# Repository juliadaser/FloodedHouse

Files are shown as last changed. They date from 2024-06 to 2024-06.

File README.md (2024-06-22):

# Flooded House

All files, code, and data used to build _**Flooded House**_.

Flooded House GIF

Art is for all! This GitHub page provides insight into my building process, and includes all files and code to make _Flooded House_ as transparent as possible. This is especially important because _Flooded House_ is a data visualization about climate change - a topic where accuracy and transparency are crucial.

## Important Links

- Read more about my project on [my website](https://www.juliadaser.com/flooded-house).
- Explore the data used for this project on [the NASA website](https://sealevel.nasa.gov/ipcc-ar6-sea-level-projection-tool).

## User Guide

1. 🛠️ Click [here](/Fabrication) for 3D models, laser files, and instructions for everything related to _**Fabrication**_.
2. 💡 Click [here](/Electronics) for circuit diagrams, instructions, and all materials used for the _**Electronics**_.
3. 💻 Click [here](/Electronics/Code) for the _**Arduino Code**_.
4. 📈 Click [here](/Downloaded%20NASA%20Data) to access the _**raw data**_ downloaded from the NASA website.

## Funding

Special thanks to [#CreateCOP](https://createcophub.com/), who awarded my project third place in the #CreateCOP28 Award, as well as the [Tidal Shift Award](https://www.tidalshiftaward.com/), who awarded my project first place in their annual award for young artists' projects about climate change. Thank you to my school's [USS Material Fund](https://www.ussnewschool.com/funding-page) for helping pay for building materials, and to Maya Georgieva who also contributed to building materials.

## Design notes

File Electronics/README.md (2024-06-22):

## Part 1: Overview

Overview Illustration of Electronics

The electronic components in Flooded House have three main functions:

- The **_Interface collects_** the user's selection of the climate scenario. The selection includes six buttons, each representing a location around the world, a potentiometer with which users can select a year, and a potentiometer with which users can select a predicted temperature increase. An "Enter" button allows users to start the visualization.

- The **_Water Height Measurement_** consists of many transistors and constantly measures the water height inside the aquarium to report it back to the Arduino. (The electronics for this are not very elegant, unfortunately.)

- **_The Water System_**, made up of water pumps, transistors, and capacitors, pumps water into or out of the aquarium depending on the user selection and the water height.

Below you can find an explanation and material list for each main function. Regular electronic items like (silicone) wire, heat shrink tubes, solder, and (Wago) connectors are also needed.

## Part 2: Interface

Pretty straight forward: A bunch of buttons, sliding potentiometers, 7-segment displays and LEDs. 

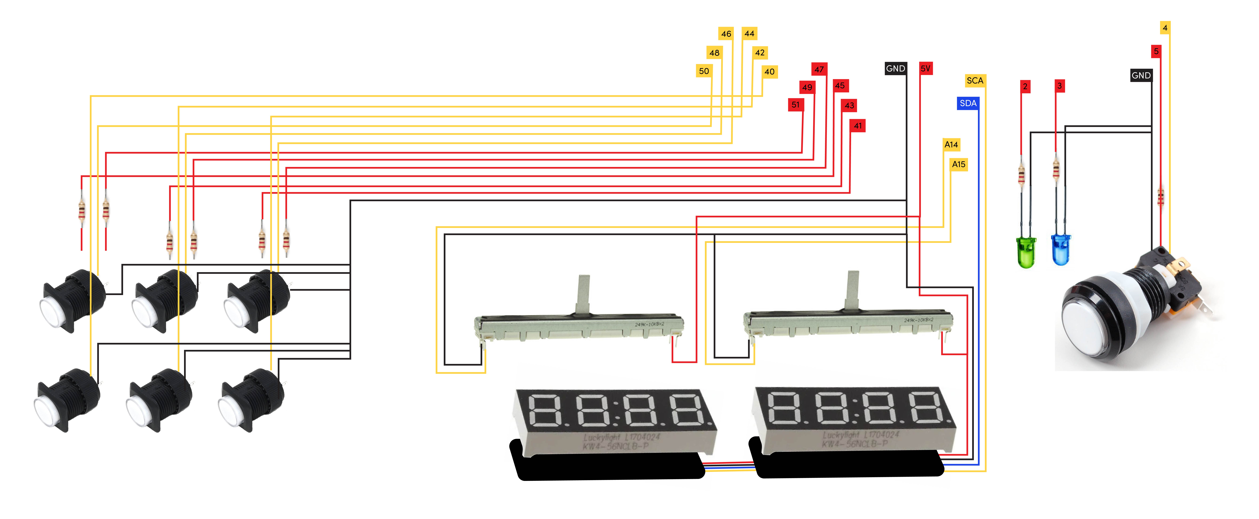
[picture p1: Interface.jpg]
Overview Illustration of Electronics


- 2 x [Sliding Potentiometers](https://www.adafruit.com/product/4219)
- 6 x [Illuminated Pushbutton](https://www.adafruit.com/product/1479)
- 2 x [7-segment display with I2C Backpack](https://www.adafruit.com/product/1002)
- 2 x [Stemma QT-connector wires](https://www.adafruit.com/product/4210)
- 1 x [Arcade Button](https://www.adafruit.com/product/492)
- 2 x Regular 4mm LED's in Blue and Green
- 2 x 220Ω Resistor for LED

## Part 3: Water Height Measurement

_Note: The way I am measuring the water height in this project is not ideal. I am measuring the water height at intervals of 5mm by placing wire ends into the aquarium at those height intervals: the first wire is placed 5mm above the floor, the second one at 10mm, and so on. A separate wire, charged with 5V, is also placed in the water at the other corner of the aquarium. If the water rises, it connects the 5V-charged wire to the other wire ends. Using transistors, I can amplify the current and detect whether the water is connecting that "circuit." Hence, I can detect how high the water has risen._

_The problem with this method is that over time multiple measurement points keep breaking. Additionally, the measurement is not very precise, as I can only detect increases of 5mm._

Overview Illustration of Electronics

- 1 x [extra thin prototyping wire](https://www.adafruit.com/product/1446)
- 22 x [2n2222a transistor](https://www.amazon.com/dp/B0CRVGFN4R?psc=1&ref=ppx_yo2ov_dt_b_product_details)

The wires marked with the 'Water' tag are placed inside the aquarium. I glued them to the back of the miniature mirror with a 5mm distance between each wire to measure the water height in 5mm intervals.
Picture of the Water Height Sensor

## Part 4: Water System

Read more about how the water pump system works [here](/../main/Fabrication/), Part 2.

_Note: I am using two separate power supplies, one for the Arduino and one for the DC water pumps. This is technically not necessary and could have been avoided by powering both the Arduino and the water pumps with 12V._

Overview Illustration of Electronics

- 2 x [mini DC 6V-12V Water Pump](https://www.amazon.com/Gikfun-Aquarium-Cooled-Diaphragm-EK1856/dp/B0744FWNFR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)
- 2 x [35V 1000uf Capacitor](https://www.amazon.com/dp/B073YR6LVK?psc=1&ref=ppx_yo2ov_dt_b_product_details)
- 2 x Transistor
- 2 x [1N4007 Diode 1A 1000V](https://www.amazon.com/MIC-Silastic-Junction-Standard-Rectifier/dp/B07GQCSC7G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)
- 1 x [12V 5A Power Supply](https://www.amazon.com/Converter-100-220V-Transformer-5-5x2-1mm-Accessories/dp/B08C594VNP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)

## Part 5: Power Supply + Putting everything together

- 1 x [Arduino Mega](https://www.amazon.com/ARDUINO-MEGA-2560-REV3-A000067/dp/B0046AMGW0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)
- 1 x [Prototyping Shield for Arduino Mega](https://www.amazon.com/KEYESTUDIO-Prototype-Board-Arduino-Double/dp/B07DRG2LN2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)
- 1 x [9V 5A Power Supply](https://www.amazon.com/dp/B08K2WJ31N?psc=1&ref=ppx_yo2ov_dt_b_product_details)
- 1x [Barrel Jack Connectors](https://www.amazon.com/dp/B08SJM2G52?psc=1&ref=ppx_yo2ov_dt_b_product_details)

## Part 6: Code!
[Find Arduino Code Here](/Electronics/Code)

## This is how my electronics looked like all put together!
Picture of finished Electronics

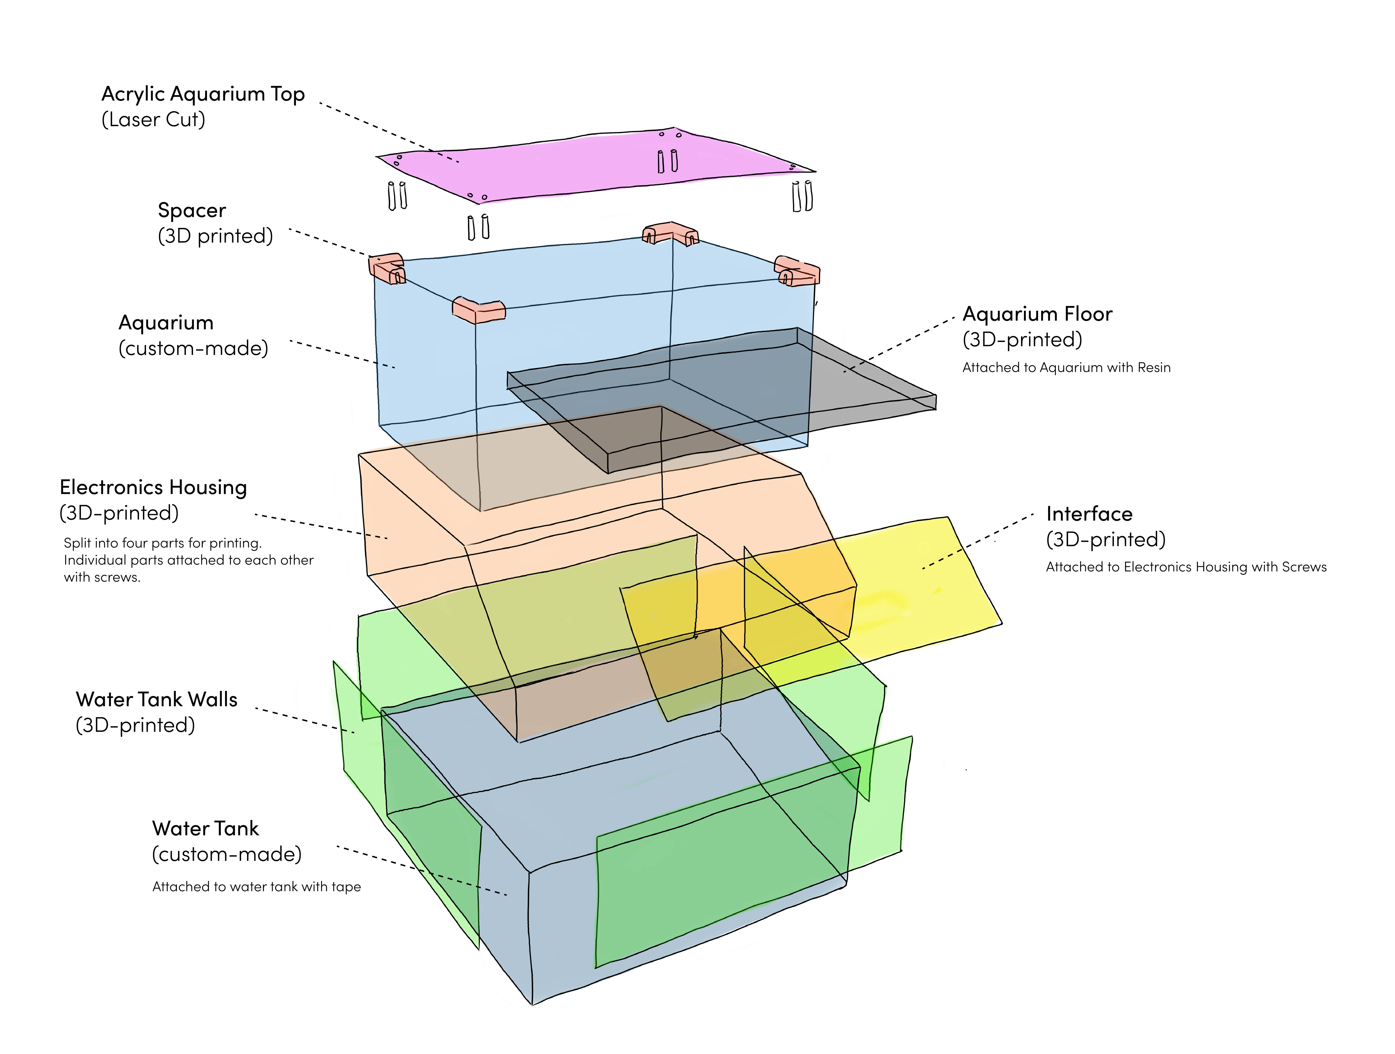
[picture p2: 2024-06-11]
Pictures/OverviewSketch.jpg

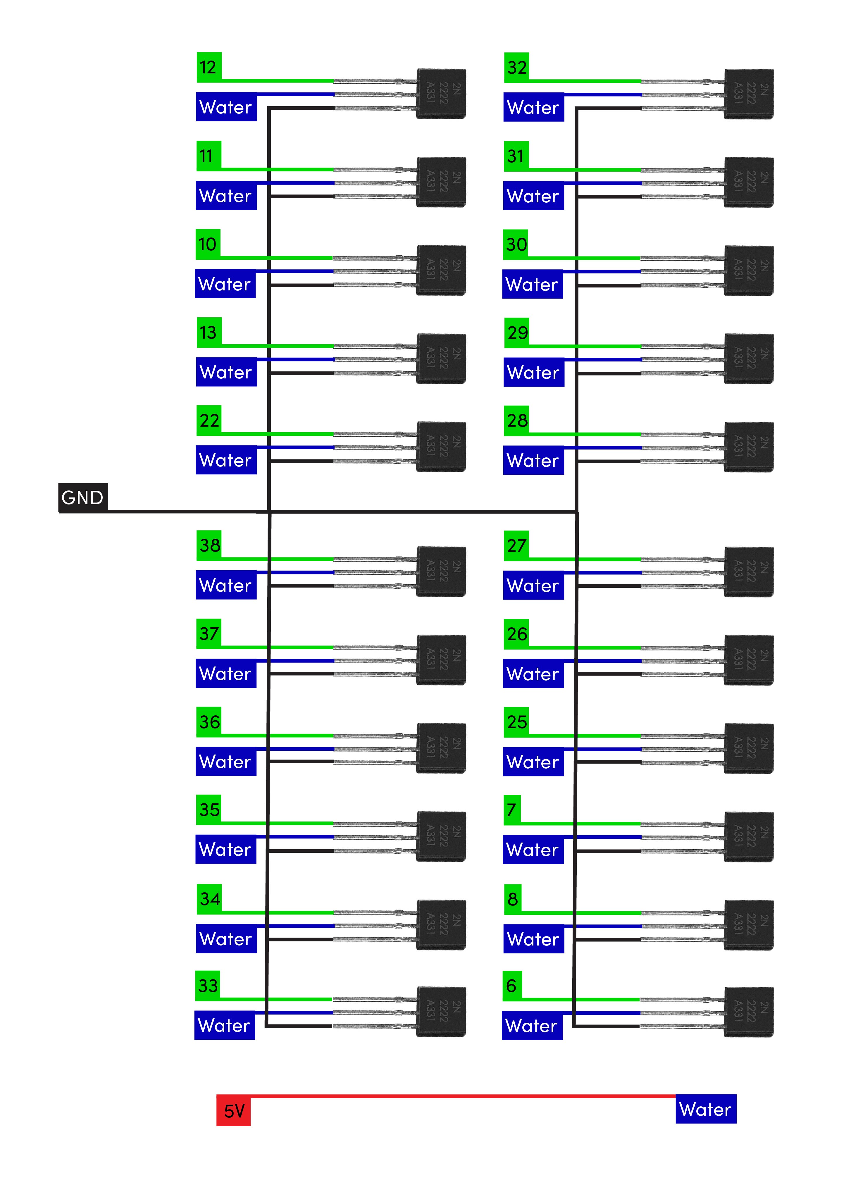
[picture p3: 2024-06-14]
Pictures/Water_Height.jpg

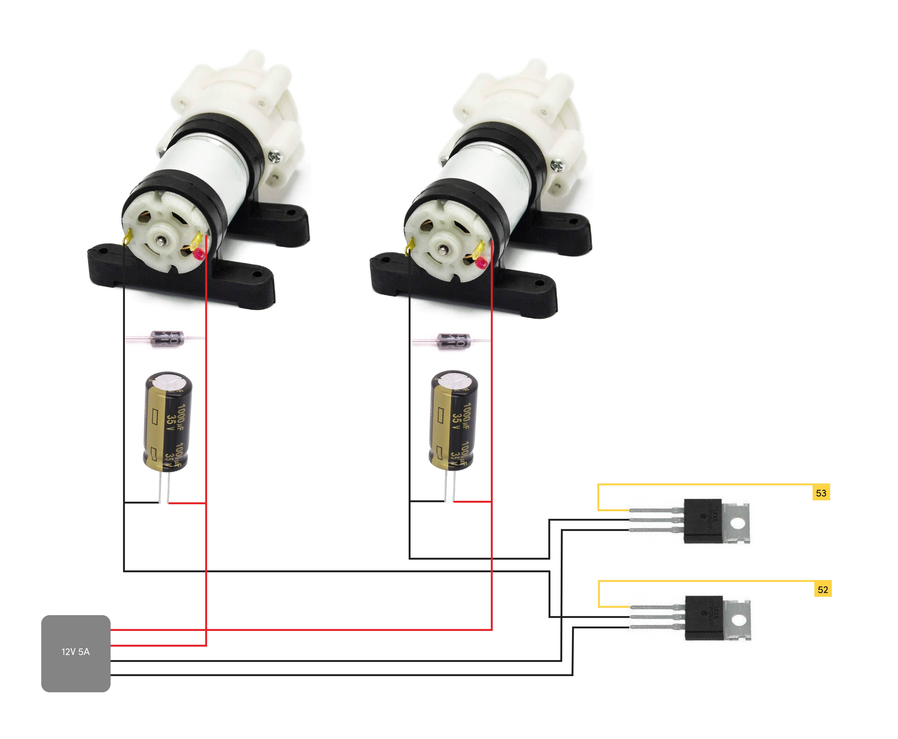
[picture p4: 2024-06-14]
Pictures/Water_System.jpg

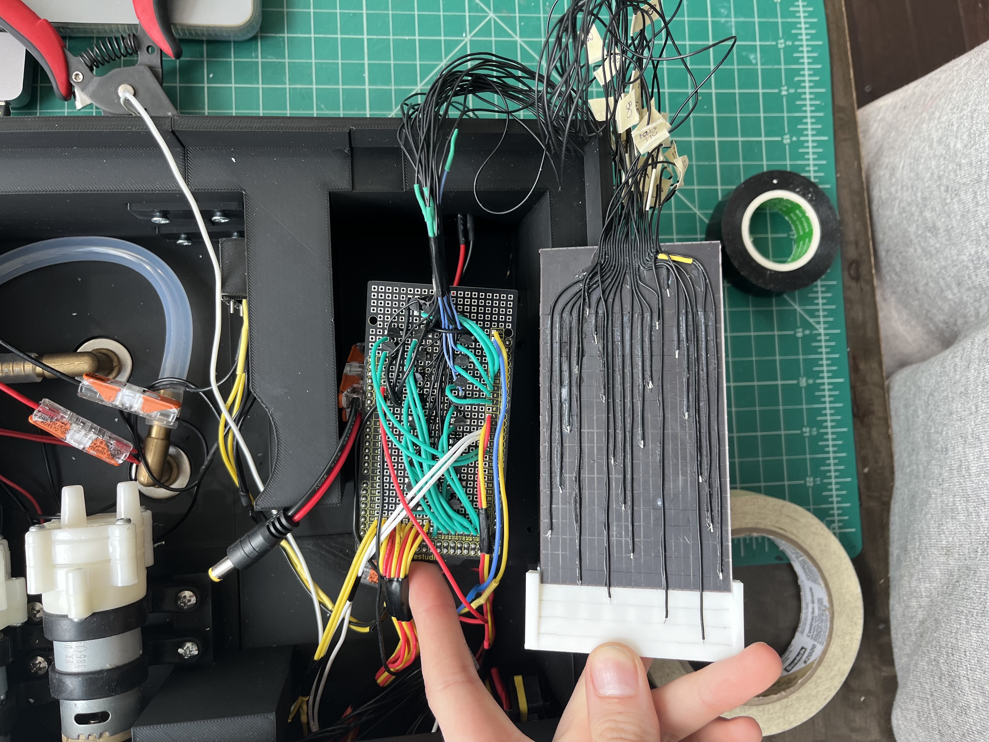
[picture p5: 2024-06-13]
Pictures/WaterHeightSensor.jpg

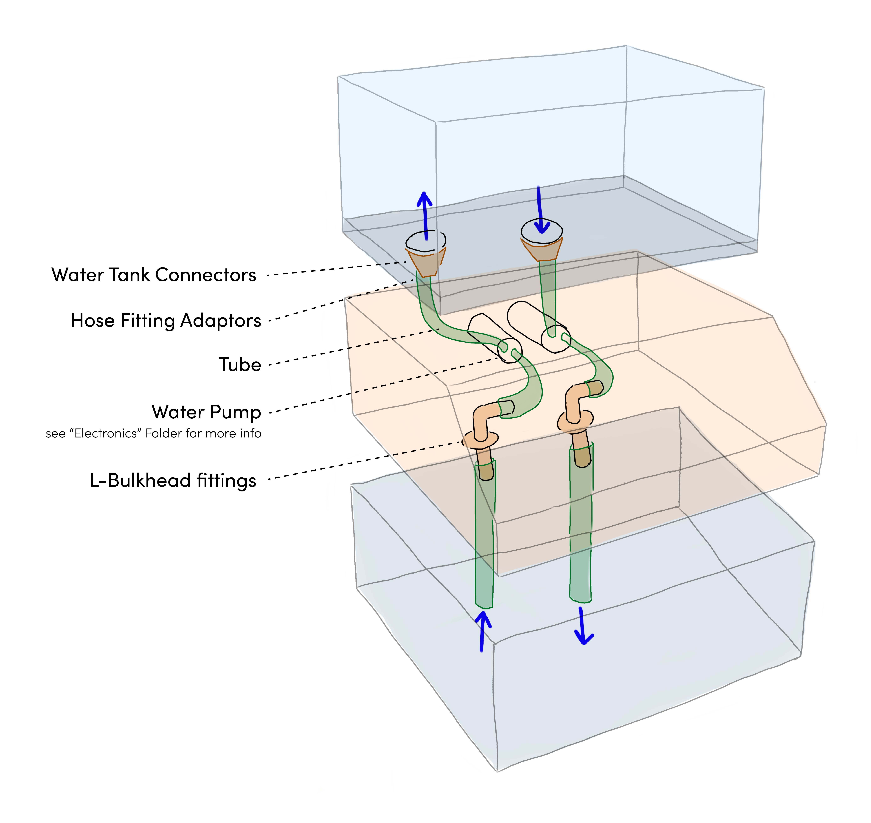
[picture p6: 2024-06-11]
Pictures/PlumbinSketch.jpg

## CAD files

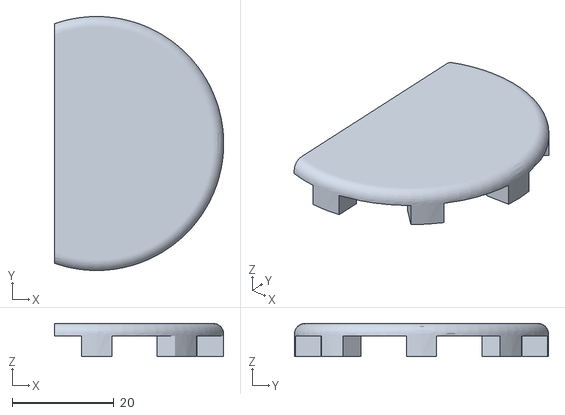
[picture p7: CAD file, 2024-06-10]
Fabrication/3D Printing/Aquarium Floor/Water Outlet Cover Corner.stl
33.4 x 50.0 x 6.50

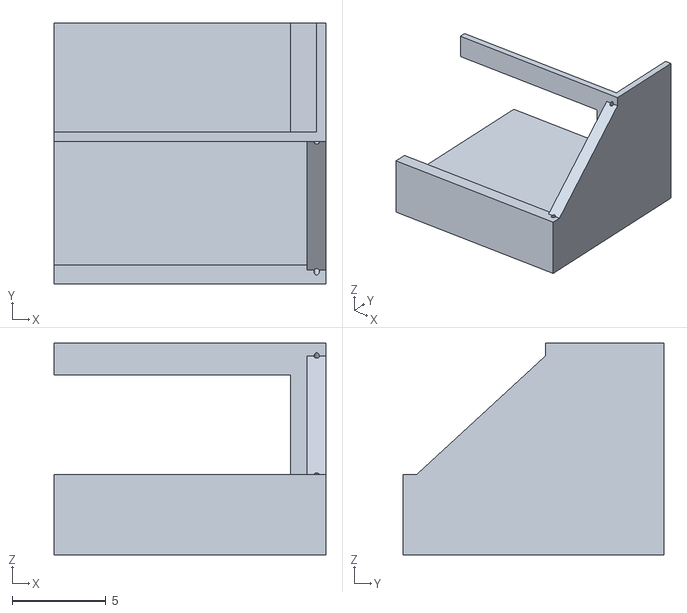
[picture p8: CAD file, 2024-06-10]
Fabrication/3D Printing/Electronics Housing/BottomRight.stl
14.5 x 13.9 x 11.3

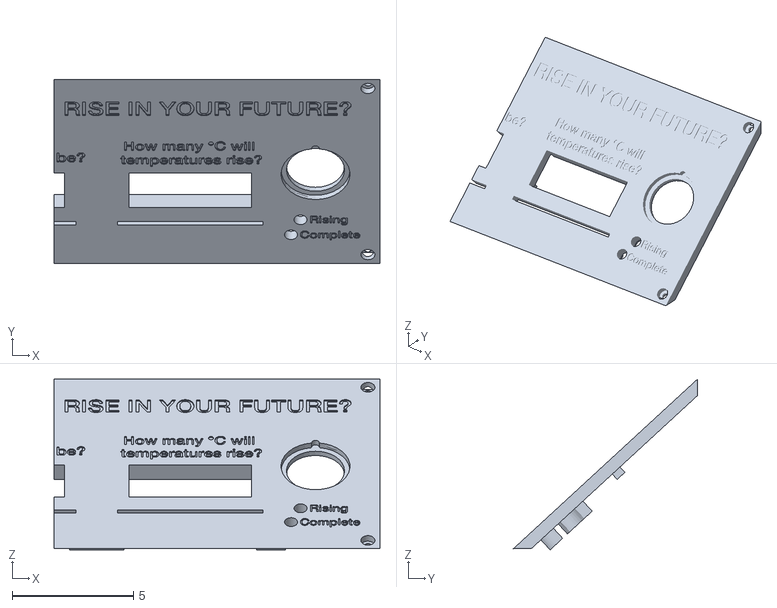
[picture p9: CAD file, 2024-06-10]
Fabrication/3D Printing/Interface/InterfaceRight.stl
13.5 x 7.60 x 7.05

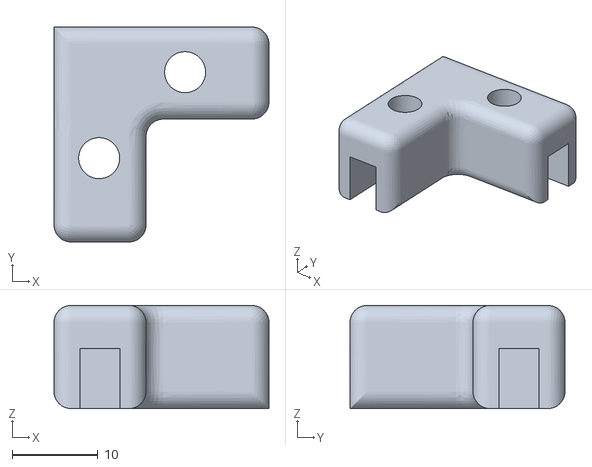
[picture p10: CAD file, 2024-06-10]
Fabrication/3D Printing/Spacer.stl
25.0 x 25.0 x 12.0

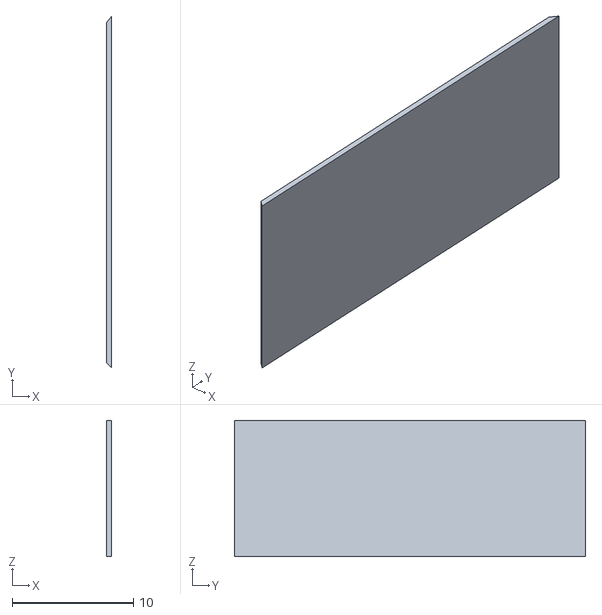
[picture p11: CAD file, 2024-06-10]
Fabrication/3D Printing/Water Tank Walls/RightWall.stl
0.4 x 29.0 x 11.2

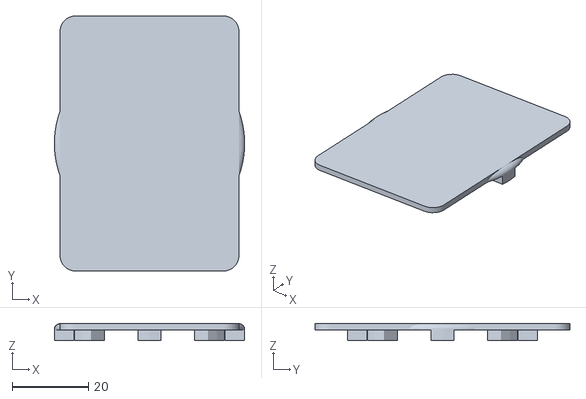
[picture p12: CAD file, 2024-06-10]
Fabrication/3D Printing/Aquarium Floor/Water Outlet Cover Center.stl
50.0 x 67.0 x 4.56

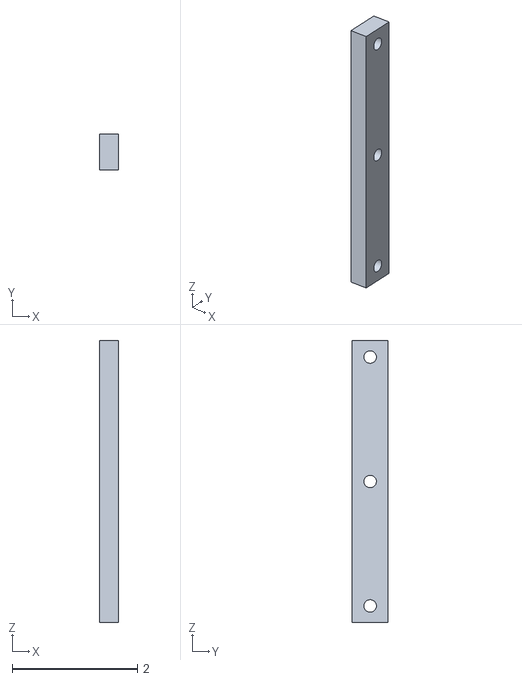
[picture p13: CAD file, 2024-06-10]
Fabrication/3D Printing/Electronics Housing/TransistorAttachment.stl
0.3 x 0.576 x 4.50

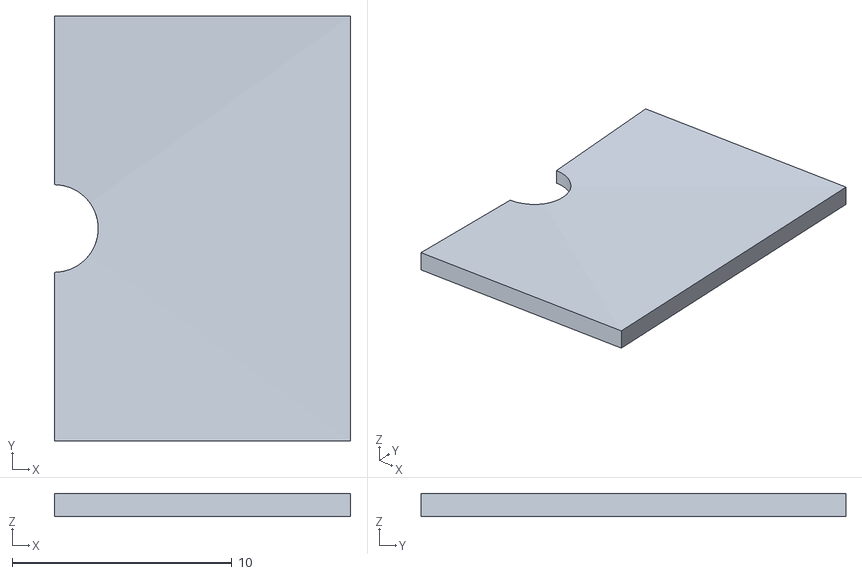
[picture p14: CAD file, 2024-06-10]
Fabrication/3D Printing/Aquarium Floor/Side Two.stl
13.5 x 19.3 x 1.06

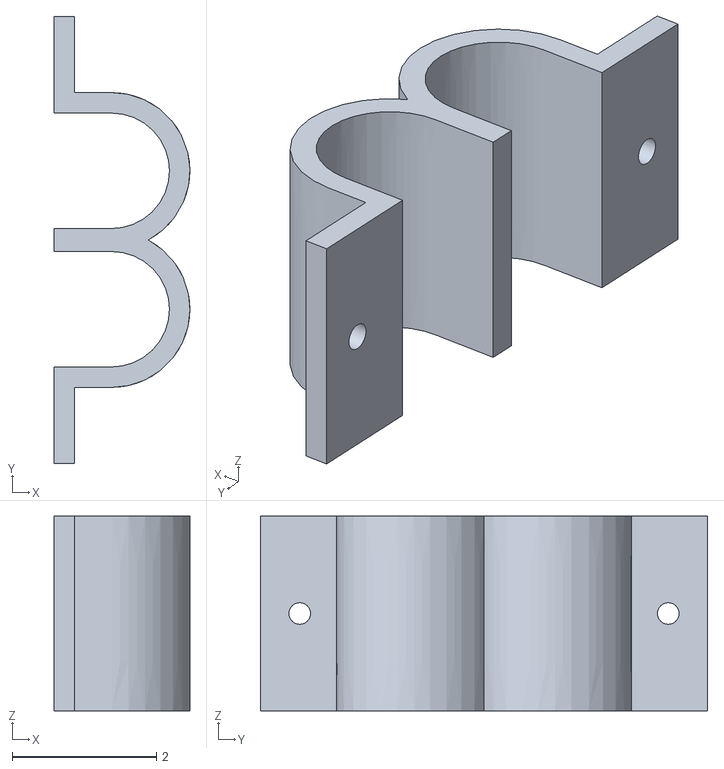
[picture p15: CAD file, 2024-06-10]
Fabrication/3D Printing/Electronics Housing/CapacitorAttachment.stl
1.88 x 6.20 x 2.70

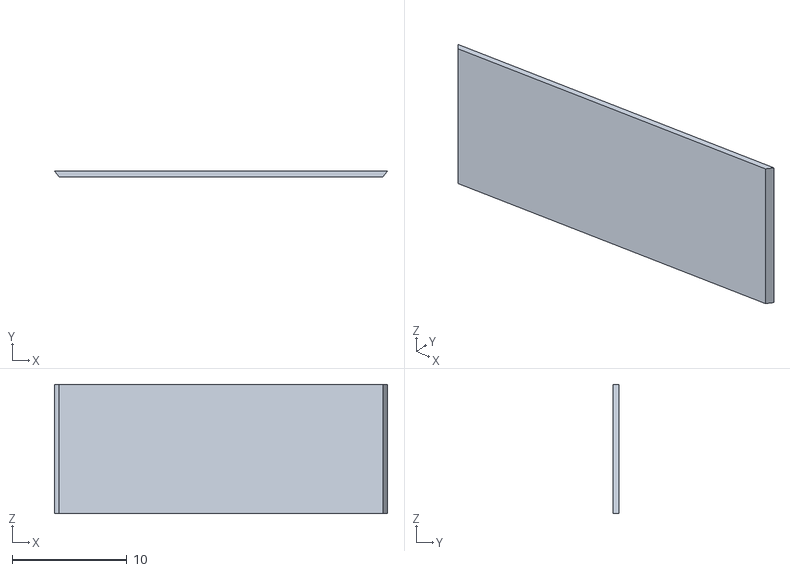
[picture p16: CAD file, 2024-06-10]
Fabrication/3D Printing/Water Tank Walls/BackWall.stl
29.0 x 0.5 x 11.2

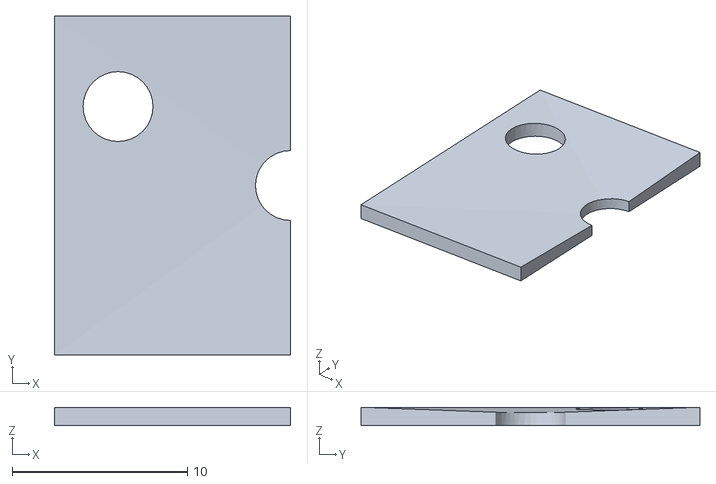
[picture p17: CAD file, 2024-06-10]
Fabrication/3D Printing/Aquarium Floor/Side One.stl
13.5 x 19.3 x 1.06

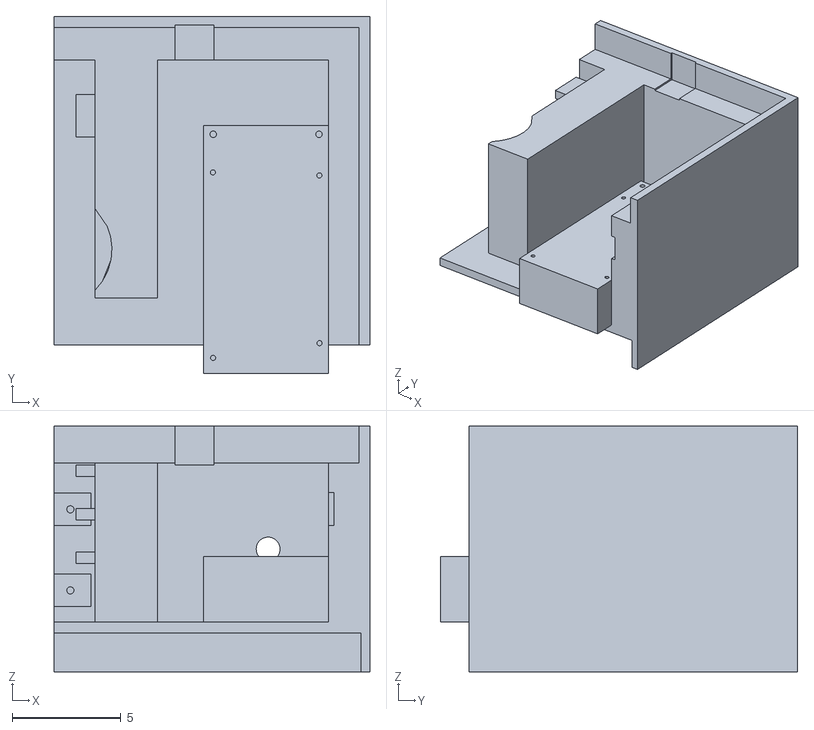
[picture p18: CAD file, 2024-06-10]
Fabrication/3D Printing/Electronics Housing/BackRight.stl
14.5 x 16.4 x 11.3

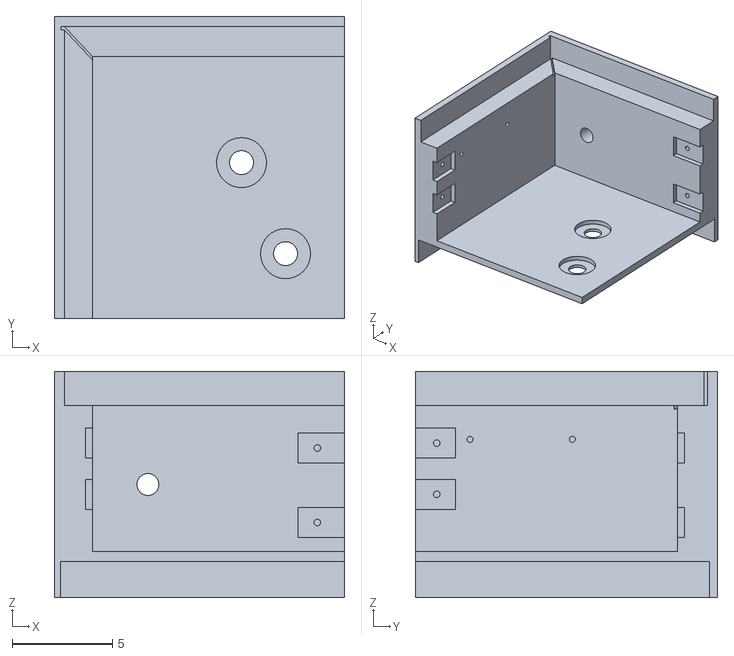
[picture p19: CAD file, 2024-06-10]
Fabrication/3D Printing/Electronics Housing/BackLeft.stl
14.5 x 15.1 x 11.3

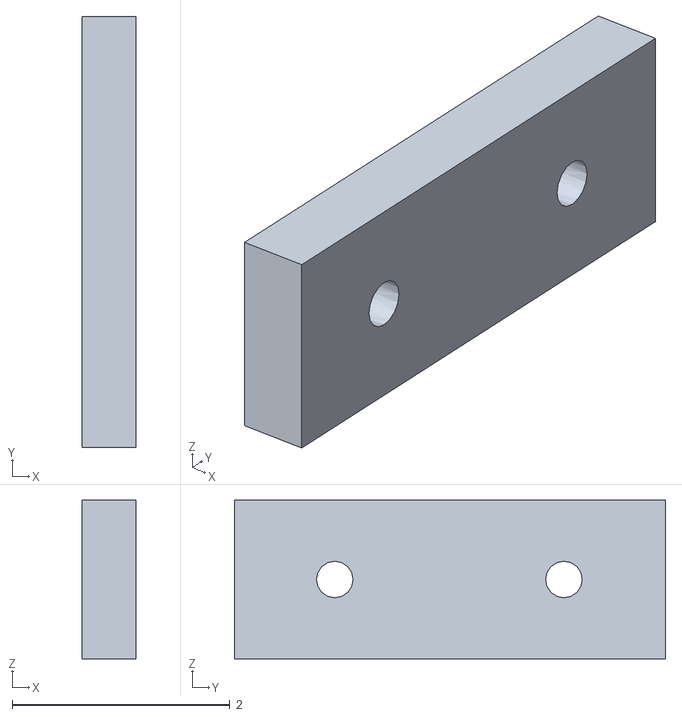
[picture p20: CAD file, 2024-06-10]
Fabrication/3D Printing/Electronics Housing/Connector.stl
0.5 x 3.96 x 1.46

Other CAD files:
Fabrication/3D Printing/Water Tank Walls/FrontWall.stl
Fabrication/3D Printing/Water Tank Walls/LeftWall.stl
Fabrication/3D Printing/Electronics Housing/FrontLeft.stl

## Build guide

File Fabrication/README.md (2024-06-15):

## Part 1: Overview
Overview Picture of Flooded House

## Part 2: Materials

### Water Storage
- [Aquarium](https://www.shoppopdisplays.com/CS001/5-sided-clear-acrylic-box-custom-size.html?list=Category%20Listing) in size 6" x 11" x 8" (HxWxD) and 3/16" wall thickness
- [Water Tank](https://www.shoppopdisplays.com/CS001/5-sided-clear-acrylic-box-custom-size.html?list=Category%20Listing) in size 5" x 11" x 11" (HxWxD) and 1/4" wall thickness

The aquarium where the miniature apartment is placed is at a 1:20 scale to my real apartment. Therefore, I had the encasings custom-made to size at ShopPOPDisplays (linked above). 

### Water System

Picture illustrating the plumbing of Flooded House.

As shown in the illustration above, there are two water pumps: one pumps water from the water tank into the aquarium, and one pumps water out of the aquarium back into the water tank. The plumbing is made waterproof using several different water tank connectors listed below. Two holes are drilled into the underside of the aquarium to fit the water tank connectors. These holes can either be laser-cut (see Part 4: Laser Cutting) or drilled with a large acrylic drill bit.

- [Silicone Tubing](https://www.amazon.com/dp/B07W5TGX8B?psc=1&ref=ppx_yo2ov_dt_b_product_details) 1/4" Inner Diameter
- Two [Water Tank Connectors](https://www.amazon.com/dp/B07GPP23K9?ref=ppx_yo2ov_dt_b_product_details&th=1) and two [Hose fitting adapters](https://www.harfington.com/products/p-1114801?variant=42673303945465) to connect the water pump to the aquarium
- Two [L-Bulkhead fittings](https://www.amazon.com/dp/B08J86HS2W?ref=ppx_yo2ov_dt_b_product_details&th=1) to connect the water tank to the water pump

## Part 3: 3D printing
[Find 3D Models here](/Fabrication/3D%20Printing)

All 3D models are provided as .stl files either in mm or cm units. Scale accordingly in your preferred 3D printing software. The _Electronics Housing_ and the _Water Tank Walls_ are printed in black filament. The _Spacers_ that hold the aquarium top are printed in transparent filament. The _Interface_ is printed in two colors: black and white, so that the text and map appear in white in the print, and the background appears in black.

## Part 4: Laser Cutting
[Find Illustrator Files here](/Fabrication/Laser%20Cutting)

The _Acrylic Aquarium Top_ is laser-cut in 1/8" thickness transparent acrylic.

## Part 5: Miniature Items

The miniature items inside the aquarium are fabricated from an array of different materials, including painted clay, wood, metal, and fabric. All items are a direct replica of my own furniture and personal items, at a scale of 1:20. Here are some pictures of what my miniature items look like:

<table>
  <tr>
    <td>
      Picture of a Miniature Item from Flooded House
    </td>
    <td>
      Picture of a Miniature Item from Flooded House
    </td>
  </tr>
  <tr>
    <td>
      Picture of a Miniature Item from Flooded House
    </td>
    <td>
      Picture of a Miniature Item from Flooded House
    </td>
  </tr>
  <tr>
    <td>
      Picture of a Miniature Item from Flooded House
    </td>
    <td>
      Picture of a Miniature Item from Flooded House
    </td>
  </tr>
</table>

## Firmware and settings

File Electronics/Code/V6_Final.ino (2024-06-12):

#include "CityData.h"
#include "Adafruit_LEDBackpack.h"

//CITY SELECTION
const int buttonPinNewYork = 50;
const int lightPinNewYork = 51;
const int buttonPinManila = 48;
const int lightPinManila = 49;
const int buttonPinKamaishi = 46;
const int lightPinKamaishi = 47;
const int buttonPinTakoradi = 44;
const int lightPinTakoradi = 45;
const int buttonPinCananeia = 42;
const int lightPinCananeia = 43;
const int buttonPinBugrino = 40;
const int lightPinBugrino = 41;

int bStateNewYork = 0;
int bStateManila = 0;
int bStateKamaishi = 0;
int bStateTakoradi = 0;
int bStateCananeia = 0;
int bStateBugrino = 0;

// DISPLAYS
Adafruit_7segment matrixYear = Adafruit_7segment();
Adafruit_7segment matrixScenario = Adafruit_7segment();

//SELECTION OF YEAR AND SCENARIO
const int potPinYear = A14;
const int potPinScenario = A15;
int potVYear = 0;
int yearDisplayValue;
int potVScenario = 0;
float scenarioDisplayValue;

// FINAL USER SELECTIONS
int selectedCity = 0;
int Scenario = 4;
int FutureYear = 2030;

//"ENTER" BUTTON
const int switchButtonPin = 4;
const int lightswitchButton = 5;
int switchButtonState = 0;
int switchButtonStateOld = 0;

// USER STAGES
bool measureOnce = true;
bool userStage = true;
bool filling = true;

//LED FEEDBACK
const int doneLED = 2;
const int waterLED = 3;

//WATERLEVEL
float waterLevelRise; // this is a variable for the NASA data
int waterLevelRiseScaled;

//HEIGHT MEASUREMENT
int waterLevel;

const int waterlevelMaxPin = 9;
int waterlevelMax;

const unsigned long maxDurationToFill = 171000; // it takes max 171 seconds to fill up the entire aquarium

const int heightPin05 = 12;
int height05;
const int heightPin10 = 11;
int height10;
const int heightPin15 = 10;
int height15;
const int heightPin20 = 13;
int height20;
const int heightPin25 = 22;
int height25;
const int heightPin30 = 38;
int height30;
const int heightPin35 = 37;
int height35;
const int heightPin40 = 36;
int height40;
const int heightPin45 = 35;
int height45;
const int heightPin50 = 34;
int height50;
const int heightPin55 = 33;
int height55;
const int heightPin60 = 32;
int height60;
const int heightPin65 = 31;
int height65;
const int heightPin70 = 30;
int height70;
const int heightPin75 = 29;
int height75;
const int heightPin80 = 28;
int height80;
const int heightPin85 = 27;
int height85;
const int heightPin90 = 26;
int height90;
const int heightPin95 = 25;
int height95;
const int heightPin100 = 7;
int height100;
const int heightPin105 = 8;
int height105;
const int heightPin110 = 6;
int height110;

//MOTORS
const int inMotorPin = 53;
const int outMotorPin = 52;

void setup() {

  Serial.begin(9600);

  pinMode(buttonPinNewYork, INPUT_PULLUP);
  pinMode(buttonPinManila, INPUT_PULLUP);
  pinMode(buttonPinKamaishi, INPUT_PULLUP);
  pinMode(buttonPinTakoradi, INPUT_PULLUP);
  pinMode(buttonPinCananeia, INPUT_PULLUP);
  pinMode(buttonPinBugrino, INPUT_PULLUP);

  pinMode(lightPinNewYork, OUTPUT);
  pinMode(lightPinManila, OUTPUT);
  pinMode(lightPinKamaishi, OUTPUT);
  pinMode(lightPinTakoradi, OUTPUT);
  pinMode(lightPinCananeia, OUTPUT);
  pinMode(lightPinBugrino, OUTPUT);

  digitalWrite(lightPinNewYork, LOW);
  digitalWrite(lightPinManila, LOW);
  digitalWrite(lightPinKamaishi, LOW);
  digitalWrite(lightPinTakoradi, LOW);
  digitalWrite(lightPinCananeia, LOW);
  digitalWrite(lightPinBugrino, LOW);

  pinMode(switchButtonPin, INPUT_PULLUP);
  pinMode(lightswitchButton, OUTPUT);
  digitalWrite(lightswitchButton, LOW);

  pinMode(waterLED, OUTPUT);
  pinMode(doneLED, OUTPUT);
  digitalWrite(waterLED, LOW);
  digitalWrite(doneLED, LOW);

  pinMode(waterlevelMaxPin, INPUT_PULLUP);
  pinMode(heightPin05, INPUT_PULLUP);
  pinMode(heightPin10, INPUT_PULLUP);
  pinMode(heightPin15, INPUT_PULLUP);
  pinMode(heightPin20, INPUT_PULLUP);
  pinMode(heightPin25, INPUT_PULLUP);
  pinMode(heightPin30, INPUT_PULLUP);
  pinMode(heightPin35, INPUT_PULLUP);
  pinMode(heightPin40, INPUT_PULLUP);
  pinMode(heightPin45, INPUT_PULLUP);
  pinMode(heightPin50, INPUT_PULLUP);
  pinMode(heightPin55, INPUT_PULLUP);
  pinMode(heightPin60, INPUT_PULLUP);
  pinMode(heightPin65, INPUT_PULLUP);
  pinMode(heightPin70, INPUT_PULLUP);
  pinMode(heightPin75, INPUT_PULLUP);
  pinMode(heightPin80, INPUT_PULLUP);
  pinMode(heightPin85, INPUT_PULLUP);
  pinMode(heightPin90, INPUT_PULLUP);
  pinMode(heightPin95, INPUT_PULLUP);
  pinMode(heightPin100, INPUT_PULLUP);
  pinMode(heightPin105, INPUT_PULLUP);
  pinMode(heightPin110, INPUT_PULLUP);

  matrixYear.begin(0x70);
  matrixScenario.begin(0x71);

  pinMode(inMotorPin, OUTPUT);
  pinMode(outMotorPin, OUTPUT);
  digitalWrite(inMotorPin, LOW);
  digitalWrite(outMotorPin, LOW);
}

void loop() {
  switchButtonState = digitalRead(switchButtonPin);

  if (switchButtonState == LOW and switchButtonStateOld == HIGH) {
    userStage = false;
  }

  waterlevelMax = digitalRead(waterlevelMaxPin);
  if (waterlevelMax == LOW) {
    Serial.println("MAX WATER LEVEL");
    emergency();
  }

  switch (userStage) {
    case true:
      digitalWrite(lightswitchButton, LOW);
      getUserData();
      measureOnce = true;
      delay(100);
      break;
    case false:
      digitalWrite(lightswitchButton, HIGH);
      if (measureOnce) {
        getData();
        measureOnce = false;
      }
      fillAquarium();
      delay(100);
      reset();
      userStage = true;
      break;
  }
  switchButtonStateOld = switchButtonState;
}

void getUserData() {
  // Check the state of each button
  bStateNewYork = digitalRead(buttonPinNewYork);
  bStateManila = digitalRead(buttonPinManila);
  bStateKamaishi = digitalRead(buttonPinKamaishi);
  bStateTakoradi = digitalRead(buttonPinTakoradi);
  bStateCananeia = digitalRead(buttonPinCananeia);
  bStateBugrino = digitalRead(buttonPinBugrino);

  if (bStateNewYork == LOW) {
    selectedCity = 0;
  } else if (bStateManila == LOW) {
    selectedCity = 1;
  } else if (bStateKamaishi == LOW) {
    selectedCity = 2;
  } else if (bStateTakoradi == LOW) {
    selectedCity = 3;
  } else if (bStateCananeia == LOW) {
    selectedCity = 4;
  } else if (bStateBugrino == LOW) {
    selectedCity = 5;
  }


  if (selectedCity == 0) {
    digitalWrite(lightPinNewYork, HIGH);
    digitalWrite(lightPinManila, LOW);
    digitalWrite(lightPinKamaishi, LOW);
    digitalWrite(lightPinTakoradi, LOW);
    digitalWrite(lightPinCananeia, LOW);
    digitalWrite(lightPinBugrino, LOW);
  }
  else if (selectedCity == 1) {
    digitalWrite(lightPinNewYork, LOW);
    digitalWrite(lightPinManila, HIGH);
    digitalWrite(lightPinKamaishi, LOW);
    digitalWrite(lightPinTakoradi, LOW);
    digitalWrite(lightPinCananeia, LOW);
    digitalWrite(lightPinBugrino, LOW);
  }
  else if (selectedCity == 2) {
    digitalWrite(lightPinNewYork, LOW);
    digitalWrite(lightPinManila, LOW);
    digitalWrite(lightPinKamaishi, HIGH);
    digitalWrite(lightPinTakoradi, LOW);
    digitalWrite(lightPinCananeia, LOW);
    digitalWrite(lightPinBugrino, LOW);
  }
  else if (selectedCity == 3) {
    digitalWrite(lightPinNewYork, LOW);
    digitalWrite(lightPinManila, LOW);
    digitalWrite(lightPinKamaishi, LOW);
    digitalWrite(lightPinTakoradi, HIGH);
    digitalWrite(lightPinCananeia, LOW);
    digitalWrite(lightPinBugrino, LOW);
  }
  else if (selectedCity == 4) {
    digitalWrite(lightPinNewYork, LOW);
    digitalWrite(lightPinManila, LOW);
    digitalWrite(lightPinKamaishi, LOW);
    digitalWrite(lightPinTakoradi, LOW);
    digitalWrite(lightPinCananeia, HIGH);
    digitalWrite(lightPinBugrino, LOW);
  }
  else if (selectedCity == 5) {
    digitalWrite(lightPinNewYork, LOW);
    digitalWrite(lightPinManila, LOW);
    digitalWrite(lightPinKamaishi, LOW);
    digitalWrite(lightPinTakoradi, LOW);
    digitalWrite(lightPinCananeia, LOW);
    digitalWrite(lightPinBugrino, HIGH);
  }

  // Read the potentiometer values
  potVYear = analogRead(potPinYear);
  potVScenario = analogRead(potPinScenario);

  yearDisplayValue = map(potVYear, 0, 1023, 2030, 2159);
  yearDisplayValue = yearDisplayValue - (yearDisplayValue % 10); // Round down to the nearest 10
  if (potVScenario < 50) {
    scenarioDisplayValue = 1.5;
  } else {
    scenarioDisplayValue = map(potVScenario, 50, 900, 2, 5);
  }

  matrixYear.print(yearDisplayValue);
  matrixScenario.print(scenarioDisplayValue, 1);
  matrixYear.writeDisplay();
  matrixScenario.writeDisplay();

  Serial.print("City: ");
  if (selectedCity == 0) {
    Serial.print("NewYork");
  }
  else if (selectedCity == 1) {
    Serial.print("Manila");
  }
  else if (selectedCity == 2) {
    Serial.print("Kamaishi");
  }
  else if (selectedCity == 3) {
    Serial.print("Takoradi");
  }
  else if (selectedCity == 4) {
    Serial.print("Cananeia");
  }
  else if (selectedCity == 5) {
    Serial.print("Bugrino");
  }
  Serial.print("   Year: ");
  Serial.print(yearDisplayValue);
  Serial.print("   Scenario: ");
  Serial.println(scenarioDisplayValue);
}

void getData() {
  int mappedYear = mapYears(yearDisplayValue);
  int mappedScenario = mapScenario(scenarioDisplayValue);

  waterLevelRise = Cities[selectedCity][mappedYear][mappedScenario];
  waterLevelRiseScaled = waterLevelRise * 50; //( *1000 (from m to mm) /20 (for scale))

  Serial.print("Water Level Rise (m): ");
  Serial.print(waterLevelRise);
  Serial.print("    SCALED (mm): ");
  Serial.println(waterLevelRiseScaled);

  delay(1000);
}

void fillAquarium() {

  unsigned long startTime = millis();

  while (filling) {

    waterlevelMax = digitalRead(waterlevelMaxPin);
    if (waterlevelMax == LOW) {
      Serial.print("MAX WATER LEVEL");
      filling = false;
      emergency();
    }

    waterheight();

    Serial.print("waterlevel: ");
    Serial.print(waterLevel);
    Serial.print("   Scaled: ");
    Serial.println(int(waterLevelRiseScaled));

    if (waterLevel <= waterLevelRiseScaled and millis() - startTime < maxDurationToFill) {

      Serial.print("Filling    ");
      digitalWrite(inMotorPin, HIGH);

      //BLUE LED BLINKS
      digitalWrite(waterLED, HIGH);
      delay(300);
      digitalWrite(waterLED, LOW);
      delay(300);

    } else {
      digitalWrite(inMotorPin, LOW);
      Serial.print("Water Level Reached     ");

      digitalWrite(waterLED, LOW);
      digitalWrite(doneLED, HIGH);

      delay(30000); //waiting for user to see (wait 20 seconds);
      digitalWrite(doneLED, LOW);

      filling = false;
    }
  }
}

void reset() {

  Serial.println("We are resetting");

  while (!filling) {

    //BLUE LED BLINKS
    digitalWrite(waterLED, HIGH);
    delay(300);
    digitalWrite(waterLED, LOW);
    delay(300);

    waterheight();

    Serial.println(waterLevel);

    if (waterLevel > 5) {
      Serial.println("Unfilling   ");
      digitalWrite(outMotorPin, HIGH);
      delay(100);
    } else if (waterLevel <= 5) {
      filling = true;
      digitalWrite(outMotorPin, HIGH);
    }
  }

  Serial.println("DONE");
  delay(12000); // to make sure all water is out
  digitalWrite(outMotorPin, LOW);
  //resetting flags

  digitalWrite(lightPinNewYork, LOW);
  digitalWrite(lightPinManila, LOW);
  digitalWrite(lightPinKamaishi, LOW);
  digitalWrite(lightPinTakoradi, LOW);
  digitalWrite(lightPinCananeia, LOW);
  digitalWrite(lightPinBugrino, LOW);

  //resetting leds
  digitalWrite(doneLED, LOW);
}

void waterheight() {
  //  //TRANSISTOR CODE HERE (make function?)
  height05 = digitalRead(heightPin05);
  height10 = digitalRead(heightPin10);
  height15 = digitalRead(heightPin15);
  height20 = digitalRead(heightPin20);
  height25 = digitalRead(heightPin25);
  height30 = digitalRead(heightPin30);
  height35 = digitalRead(heightPin35);
  height40 = digitalRead(heightPin40);
  height45 = digitalRead(heightPin45);
  height50 = digitalRead(heightPin50);
  height55 = digitalRead(heightPin55);
  height60 = digitalRead(heightPin60);
  height65 = digitalRead(heightPin65);
  height70 = digitalRead(heightPin70);
  height75 = digitalRead(heightPin75);
  height80 = digitalRead(heightPin80);
  height85 = digitalRead(heightPin85);
  height90 = digitalRead(heightPin90);
  height95 = digitalRead(heightPin95);
  height100 = digitalRead(heightPin100);
  height105 = digitalRead(heightPin105);
  height110 = digitalRead(heightPin110);

  if (waterlevelMax == LOW) {
    waterLevel = 200;
  } else if (height110 == LOW) {
    waterLevel = 110;
  } else if (height105 == LOW) {
    waterLevel = 105;
  } else if (height100 == LOW) {
    waterLevel = 100;
  } else if (height95 == LOW) {
    waterLevel = 95;
  } else if (height90 == LOW) {
    waterLevel = 90;
  } else if (height85 == LOW) {
    waterLevel = 85;
  } else if (height80 == LOW) {
    waterLevel = 80;
  } else if (height75 == LOW) {
    waterLevel = 75;
  } else if (height70 == LOW) {
    waterLevel = 70;
  } else if (height65 == LOW) {
    waterLevel = 65;
  } else if (height60 == LOW) {
    waterLevel = 60;
  } else if (height55 == LOW) {
    waterLevel = 55;
  } else if (height50 == LOW) {
    waterLevel = 50;
  } else if (height45 == LOW) {
    waterLevel = 45;
  } else if (height40 == LOW) {
    waterLevel = 40;
  } else if (height35 == LOW) {
    waterLevel = 35;
  } else if (height30 == LOW) {
    waterLevel = 30;
  } else if (height25 == LOW) {
    waterLevel = 25;
  } else if (height20 == LOW) {
    waterLevel = 20;
  } else if (height15 == LOW) {
    waterLevel = 15;
  } else if (height10 == LOW) {
    waterLevel = 10;
  } else if (height05 == LOW) {
    waterLevel = 5;
  } else {
    waterLevel = 0;
  }
}

void emergency() {
  Serial.println("WE ARE IN AN EMERGENCY");
  digitalWrite(inMotorPin, LOW);
  delay(5000);
  reset();
  userStage = true;
}

int mapYears(int inputYear) {
  int mappedValue = (inputYear - 2030) / 10;
  mappedValue = constrain(mappedValue, 0, 12);
  return mappedValue;
}

int mapScenario(float inputScenario) {
  if (inputScenario == 1.5) {
    int mappedValue = 0;
    return mappedValue;
  } else {
    int mappedValue = (int)((inputScenario - 1));
    mappedValue = constrain(mappedValue, 0, 4);
    return mappedValue;
  }
}

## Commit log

2024-06-13 Rename Wiring Diagram.jpg to Pictures/Wiring Diagram.jpg
2024-06-14 Update and rename Flooded House Data - Manila, (metric).csv to Flooded House Data - Manila (metric).csv
    [Flooded House Data - Manila (metric).csv]
